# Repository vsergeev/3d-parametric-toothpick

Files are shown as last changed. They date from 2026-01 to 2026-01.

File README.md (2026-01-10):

# Parametric Toothpick Frame

<table>
<tr>
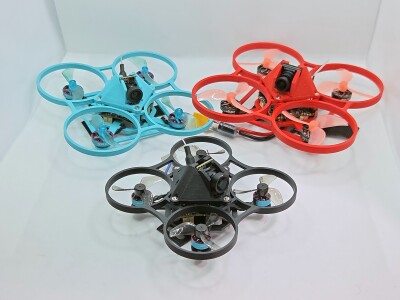
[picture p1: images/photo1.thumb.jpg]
<td></td>
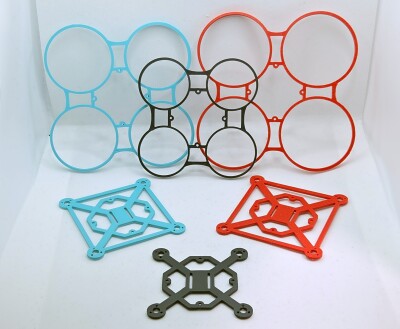
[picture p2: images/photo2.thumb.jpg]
<td></td>
</tr>
<tr>
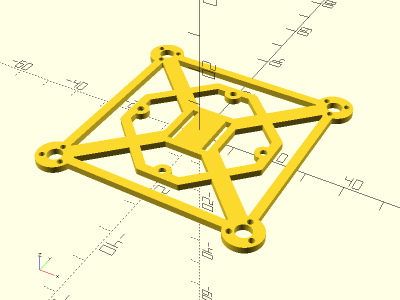
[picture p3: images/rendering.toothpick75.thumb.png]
Toothpick 75mm Rendering
<td></td>
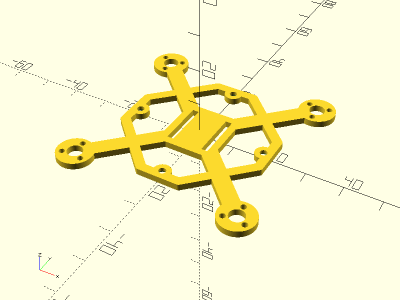
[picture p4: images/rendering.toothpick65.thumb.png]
Toothpick 65mm Rendering
<td></td>
</tr>
<tr>
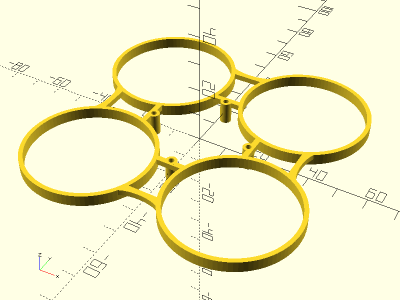
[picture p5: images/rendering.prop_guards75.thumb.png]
Prop Guard 75mm Rendering
<td></td>
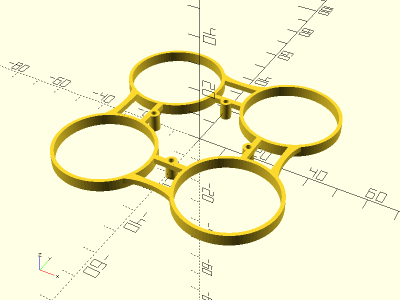
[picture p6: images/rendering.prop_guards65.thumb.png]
Prop Guard 65mm Rendering
<td></td>
</tr>
</table>

A parametric micro toothpick frame with optional prop guards. Compatible with canopies from the [Parametric Whoop Canopy](https://github.com/vsergeev/3d-parametric-whoop-canopy) project. Battery is secured to frame with velcro strap. Made with OpenSCAD.

This frame improves on the durability and printability of the [Parametric Whoop](https://github.com/vsergeev/3d-parametric-whoop) project. It has less structural features on the Z-axis, like motor struts or the battery cage, which were prone to breaking on impact. It also prints flat, with no supports, in under one hour.

**Base Designs**

* [`toothpick.scad`](toothpick.scad) - Toothpick Frame
* [`prop_guards.scad`](prop_guards.scad) - Prop Guards

**Instances**

* [`65mm_26x26_toothpick.scad`](65mm_26x26_toothpick.scad) - 65mm Toothpick Frame with 26mm mounting holes (weight 1.9g ASA)
* [`75mm_26x26_toothpick.scad`](75mm_26x26_toothpick.scad) - 75mm Toothpick Frame with 26mm mounting holes (weight 2.9g ASA)
* [`80mm_26x26_toothpick.scad`](80mm_26x26_toothpick.scad) - 80mm Toothpick Frame with 26mm mounting holes (weight 3.5g ASA)
* [`65mm_26x26_prop_guards.scad`](65mm_26x26_prop_guards.scad) - 65mm Prop Guards with 26mm mounting holes (weight 2.7g ASA)
* [`75mm_26x26_prop_guards.scad`](75mm_26x26_prop_guards.scad) - 75mm Prop Guards with 26mm mounting holes (weight 3.8g ASA)
* [`80mm_26x26_prop_guards.scad`](80mm_26x26_prop_guards.scad) - 80mm Prop Guards with 26mm mounting holes (weight 5.4g ASA)

**Recommended Print Settings:** ASA / PETG for frame, ASA / PETG / Hard TPU for prop guards, 0.20mm layer height, 100% infill, no supports. Print frame and prop guards upside down.

**Printables:** https://www.printables.com/model/1551047-parametric-toothpick-frame

**Thingiverse:** https://www.thingiverse.com/thing:7267710

## Builds

### 65mm BETAFPV Matrix 1S 5in1 (Analog VTX) + BETAFPV C03 Camera

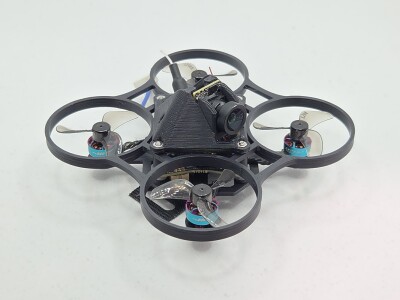
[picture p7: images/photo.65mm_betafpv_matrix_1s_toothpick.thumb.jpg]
65mm BETAFPV Matrix 1S Toothpick


* Frame: [65mm_26x26_toothpick.stl](stl/65mm_26x26_toothpick.stl)
* Prop Guards: [65mm_26x26_prop_guards.stl](stl/65mm_26x26_prop_guards.stl)
* Canopy: [betafpv_c03_26x26_canopy.5deg.stl](https://github.com/vsergeev/3d-parametric-whoop-canopy/blob/master/stl/betafpv_c03_26x26_canopy.5deg.stl)
* Flight Controller: [BETAFPV Matrix 1S](https://betafpv.com/collections/brushless-flight-controller/products/matrix-1s-brushless-flight-controller)
* Camera: [BETAFPV C03 Camera](https://betafpv.com/products/c03-fpv-micro-camera)
* Motors: RCinPower 0702 27000KV
* Props: Gemfan 1210-2 31mm
* Hardware:
    * 12x M1.4x3 for motors (included with motors)
    * 4x 2mm tall spacers: [4x2mm_spacer.stl](stl/4x2mm_spacer.stl)
    * 4x M1.6 nuts and 4x M1.6x16 bolts for frame

Total Weight without battery: 23.9g ASA

### 75mm BETAFPV Matrix 1S 5in1 (Analog VTX) + BETAFPV C03 Camera

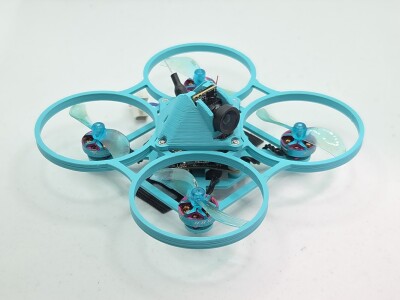
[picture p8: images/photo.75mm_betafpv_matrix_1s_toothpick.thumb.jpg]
75mm BETAFPV Matrix 1S Toothpick


* Frame: [75mm_26x26_toothpick.stl](stl/75mm_26x26_toothpick.stl)
* Prop Guards: [75mm_26x26_prop_guards.stl](stl/75mm_26x26_prop_guards.stl)
* Canopy: [betafpv_c03_26x26_canopy.5deg.stl](https://github.com/vsergeev/3d-parametric-whoop-canopy/blob/master/stl/betafpv_c03_26x26_canopy.5deg.stl)
* Flight Controller: [BETAFPV Matrix 1S](https://betafpv.com/collections/brushless-flight-controller/products/matrix-1s-brushless-flight-controller)
* Camera: [BETAFPV C03 Camera](https://betafpv.com/products/c03-fpv-micro-camera)
* Motors: RCinPower GTS V3 1002 19000KV
* Props: Gemfan 1610-2 40mm
* Hardware:
    * 12x M1.4x3 for motors (included with motors)
    * 4x 2mm tall spacers: [4x2mm_spacer.stl](stl/4x2mm_spacer.stl)
    * 4x M1.6 nuts and 4x M1.6x16 bolts for frame

Total Weight without battery: 30.2g ASA

### 80mm HDZero AIO15 (Digital VTX) + HDZero Lux Camera

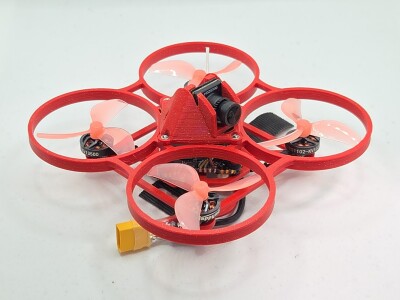
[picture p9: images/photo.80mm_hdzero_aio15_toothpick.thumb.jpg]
80mm HDZero AIO15 Toothpick


* Frame: [80mm_26x26_toothpick.stl](stl/80mm_26x26_toothpick.stl)
* Prop Guards: [80mm_26x26_prop_guards.stl](stl/80mm_26x26_prop_guards.stl)
* Canopy: [hdzero_lux_26x26_canopy.5deg.stl](https://github.com/vsergeev/3d-parametric-whoop-canopy/blob/master/stl/hdzero_lux_26x26_canopy.5deg.stl)
* Flight Controller: [HDZero AIO15](https://www.hd-zero.com/product-page/hdzero-aio15)
* Camera: [HDZero Lux Camera](https://www.hd-zero.com/product-page/hdzero-lux-camera)
* Motors: Happymodel RS1102 13500KV
* Props: Gemfan 45mm-3
* Hardware:
    * 12x M1.4x4 for motors (included with motors)
    * 4x M1.6 nuts and 4x M1.6x18 bolts for frame

Total Weight without battery: 40.3g ASA

## License



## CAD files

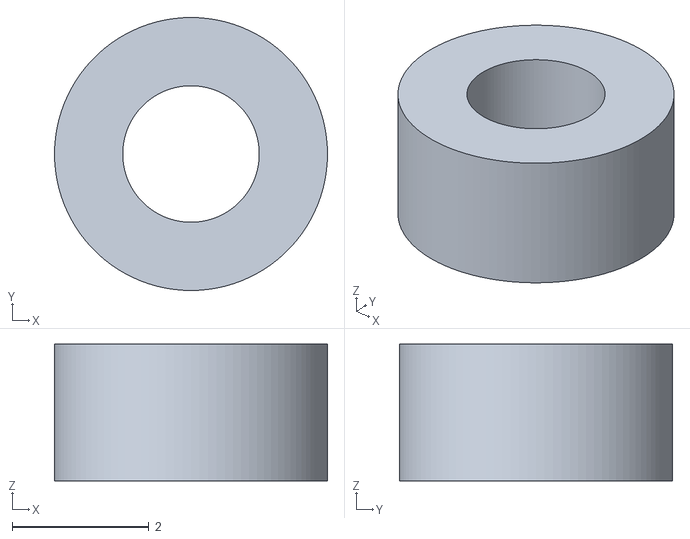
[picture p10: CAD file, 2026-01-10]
stl/4x2mm_spacer.stl
4.00 x 4.00 x 2.00

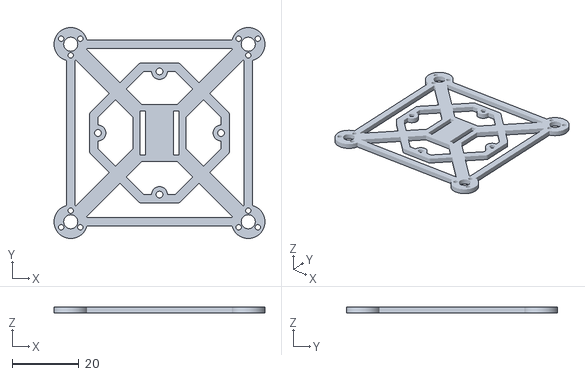
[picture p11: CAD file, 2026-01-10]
stl/75mm_26x26_toothpick.stl
63.0 x 63.0 x 1.80

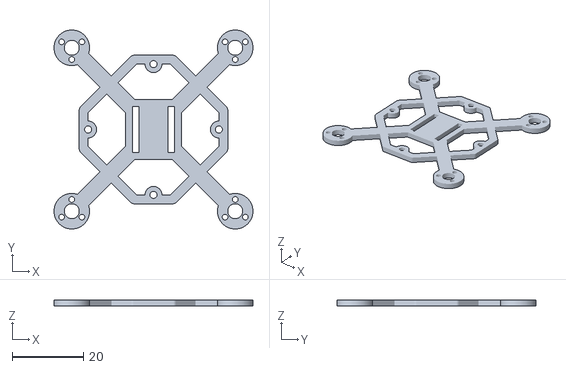
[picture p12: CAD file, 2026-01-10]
stl/65mm_26x26_toothpick.stl
56.0 x 56.0 x 1.80

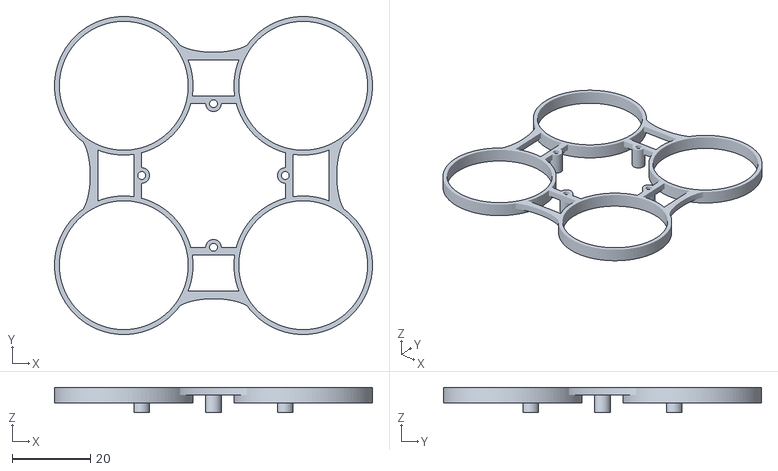
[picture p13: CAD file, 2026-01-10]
stl/65mm_26x26_prop_guards.stl
81.5 x 81.5 x 6.50

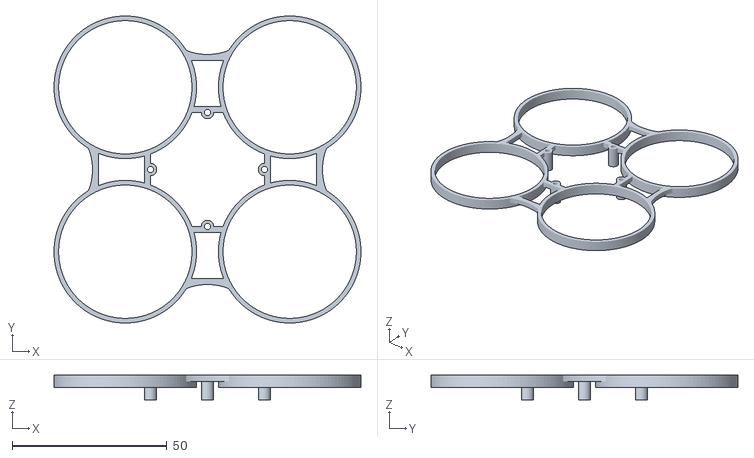
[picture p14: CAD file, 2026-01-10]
stl/75mm_26x26_prop_guards.stl
99.0 x 99.0 x 8.00

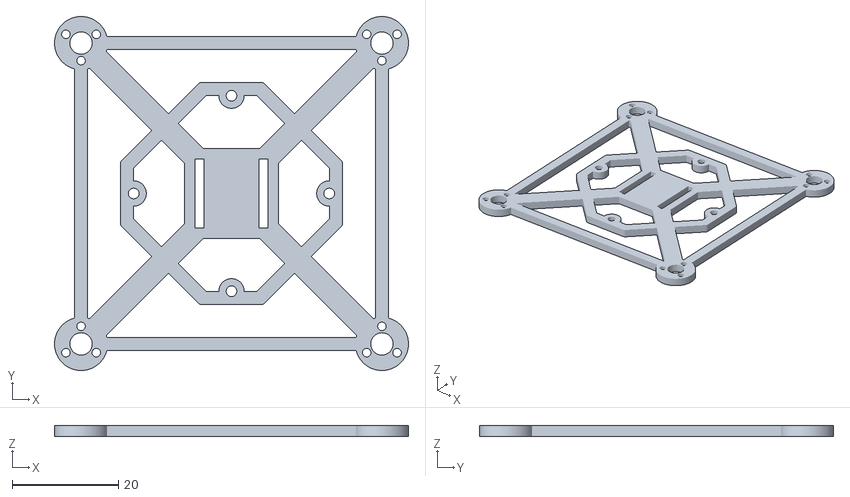
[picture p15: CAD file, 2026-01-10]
stl/80mm_26x26_toothpick.stl
66.6 x 66.6 x 2.00

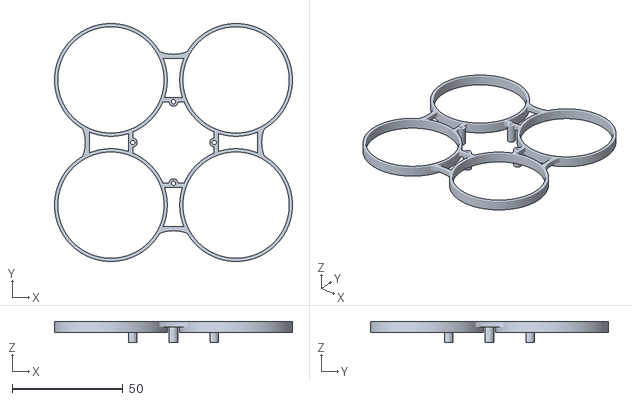
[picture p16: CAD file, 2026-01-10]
stl/80mm_26x26_prop_guards.stl
107.6 x 107.6 x 9.50

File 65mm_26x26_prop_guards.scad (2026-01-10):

include <prop_guards.scad>;

// Dimensional changes
prop_guard_xy_wheelbase = 65;
prop_guard_xy_diameter = 33;
prop_guard_xy_thickness = 1.25;
spacer_z_height = 6.5;

prop_guard();

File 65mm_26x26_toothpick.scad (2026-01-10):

include <toothpick.scad>;

// Dimensional changes
toothpick_xy_wheelbase = 65;
support_crossbar_enabled = false;

toothpick();

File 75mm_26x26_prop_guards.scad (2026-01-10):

include <prop_guards.scad>;

// Default parameters are for 75mm prop guard

prop_guard();

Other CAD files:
75mm_26x26_toothpick.scad
80mm_26x26_prop_guards.scad
80mm_26x26_toothpick.scad
prop_guards.scad
spacer.scad
toothpick.scad

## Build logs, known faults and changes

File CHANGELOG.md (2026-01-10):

* v1.0 - 01/09/2026
    * Initial release.

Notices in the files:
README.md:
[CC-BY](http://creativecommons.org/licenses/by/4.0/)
